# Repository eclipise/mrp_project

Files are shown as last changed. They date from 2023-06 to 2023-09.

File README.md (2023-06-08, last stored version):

# Program Overview

The program’s GUI is implemented with PySimpleGUI in the `GUI` class of the `remote_app.py` file, which is also the main file to run for the remote application. When run, it creates a new object `gui` of the `GUI` class, which internally creates an object `client` of the `Client` class. On creation, `gui` generates a popup window prompting for the IP address of the server, erroring and re-prompting if the IP address is invalid or cannot be reached. Afterwards, it creates the main GUI window.

When the user presses one of the movement buttons on the GUI, the `gui` object calls the `send_movement` method of `gui.client`, which sends the appropriate movement command to the server using an HTTP POST request to the `/move` endpoint. 

The server is implemented in the `server.py` file using Flask, which is the main file running on the Jetson Nano. Upon receiving a POST to `/move`, the server validates the received JSON, checking that the three required fields, `move`, `turn`, and `duration` are present and in valid ranges (-100 to 100 for `move` and `turn`, greater than 0 for `duration`). If they are not valid, the server responds with code 400 and a list of the errors. If they are valid, the server passes them on to the Arduino using the `send_movement` method of an object `arduino_controller` of class `ArduinoController`, which is implemented in `arduino_controller.py`

The `main.iso` file, running on the Arduino, waits indefinitely for an incoming serial message. When it receives one and takes action, it responds with an arbitrary number of serial messages separated by newlines, ending communication with a sentinel message that begins with `END`. For example, its response may be: 

```
Status: Moving robot with command <speed: 100, turn: 0, duration: 200>\n
Info: Left motor speed: 255; right motor speed: 255\n
Status: Robot stopped\n
END: Success\n
```

Or, on failure:

```
Status: Moving robot with command <speed: -100, turn: 0, duration: 200>\n
Abort: Back is not clear\n
END: Failure\n
```

`ArduinoController` continues monitoring the serial connection and catching messages until it receives the sentinel message. 

On receiving a command in its `loop` function, the Arduino performs its own checks on the values (which is redundant but good practice). If the values fail this check, the Arduino responds with the errors and waits for another message. If they pass, it calls its own `moveRobot` function, which checks if the robot is clear to move and moves it if it is. The duration of the movement command is handled by a loop that iterates every 10 ms, stopping the robot if it is no longer clear to move or if the current time is at least `duration` ms from the time the movement started. If the movement completed uninterrupted, `moveRobot` returns 0, else it returns 1 (which `loop` uses to determine whether to send "END: Success" or "END: Failure").

The logic that checks if the robot is clear to move is in `main.ino`'s `frontClear`, `backClear`, and `areaClear` functions, which each update the data from the IR sensors before executing. `frontClear` checks if the front left and right sensors are clear to 30 cm, and if the front center sensor is clear to 20 cm. `backClear` checks if the rear left and right sensors are clear to 30 cm. `areaClear` is used for turning and checks if all sensors are clear to 10 cm. These three functions are called from the `checkClear` function, which takes `speed` and `turn` values and performs the appropriate check based on them. 

After the Arduino finishes and `ArduinoController` receives the sentinel message, it returns a list of the messages to the server, which sends them back to the client using an HTTP response with code 200. The client passes them unchanged to the GUI, which at present prints them to the console.

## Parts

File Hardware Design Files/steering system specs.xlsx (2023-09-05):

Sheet: Motor Specs 6in wheels
Parameters | # | Units |  |  |  |  |  | Input Value
Weight of robot: | 200 | lbs | 90.70 | kg |  |  |  | Output Value
Max Speed: | 100 | ft/min | 1.666666667 | ft/s | 0.508 | m/s
Max incline to climb: | 5 | degrees
Reach max speed in seconds: | 1 | s | 0.508 | m/s^2
Drive wheel diameter: | 6 | in | 3 | in (radius) | 0.0762 | m (radius)
Torque: | 9.41 | Nm | 83.39548646 | in-lbs | 96.0004059 | kg.cm
Per motor with 2 drive motors | 4.707211903 | Nm | 41.69774323 | in-lbs | 48.00020295 | kg.cm
Per motor with 4 drive motors | 2.353605951 | Nm | 20.84887162 | in-lbs | 24.00010148 | kg.cm
rotational speed: | 63.66197724 | RPM | 6.666666667 | rad/sec
Power: | 62.76282537 | watts
Horsepower: | 0.08413247369
Horsepower per motor, 2WD | 0.04206623684
Horsepower per motor, 4WD | 0.02103311842
For payload |  |  |  |  | For incline |  |  |  | For speed
Selected motor torque: | 2.5 | Nm |  |  | Selected motor torque: | 2.5 | Nm |  | Selected motor torque: | 2.5 | Nm
robot acceleration: | 0.5 | m/s2 |  |  | robot acceleration: | 0.05 | m/s2 |  | robot acceleration: | 2 | m/s2
incline angle: | 2.5 | degrees |  |  | incline angle: | 20 | degrees |  | incline angle: | 5 | degrees
wheel radius: | 0.0762 | m |  |  | wheel radius: | 0.1524 | m |  | wheel radius: | 0.1524 | m
safty factor: | 1.5 |  |  |  | safty factor: | 1.5 |  |  | safty factor: | 1.5
1WD Robot weight: | 51.99989936 | lbs |  |  | 1WD Robot weight: | 7.088656484 | lbs |  | 1WD Robot weight: | 8.448880979 | lbs
2WD Robot weight: | 103.9997987 | lbs |  |  | 2WD Robot weight: | 14.17731297 | lbs |  | 2WD Robot weight: | 16.89776196 | lbs
4WD Robot weight: | 207.9995974 | lbs |  |  | 4WD Robot weight: | 28.35462593 | lbs |  | 4WD Robot weight: | 33.79552391 | lbs
Citation: | https://www.servomagazine.com/magazine/article/tips_for_selecting_dc_motors_for_your_mobile_robot

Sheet: Battery Size
Item name | mA | Quantity | Parts total
Motors | 3500 | 4 | 14000
computer | 3000 | 1 | 3000 |  | Battery capacity (mAh) | 30000
wifi chip | computer | 1 |  |  | Battery life (hr): | 1.488833747
ir sensor | 30 | 5 | 150
laser scanner | computer | 1
Arduino | 3000 | 1 | 3000
 |  | total | 20150 | mA
 |  |  | assuming everything is running at max

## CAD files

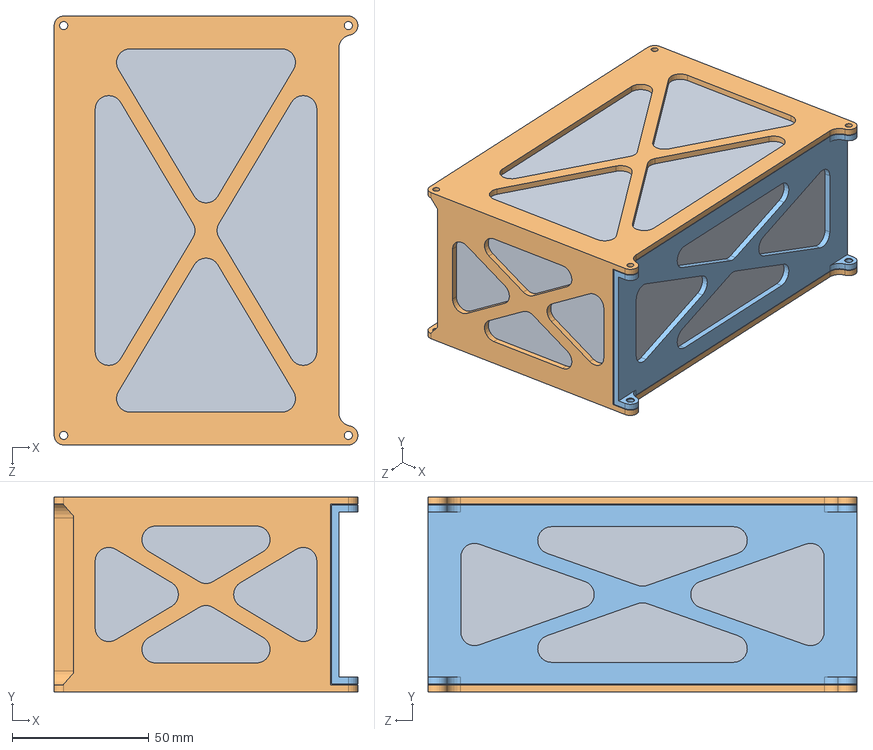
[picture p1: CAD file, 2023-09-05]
Hardware Design Files/2.2 Power Management System/2.2.8 LiFePO4 Batteries/BatteryCell.SLDASM
111.1 x 71.3 x 156.9 mm
Battery
BatteryCarrier
BatteryCarrier - Lid

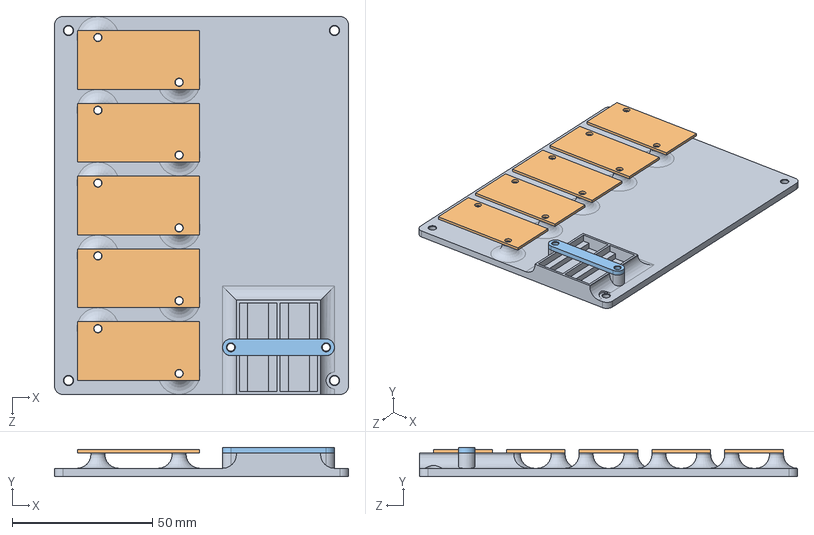
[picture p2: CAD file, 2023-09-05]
Hardware Design Files/2.3 Control System/2.3.1 Buck Converter Assembly/BuckConverter Assembly.SLDASM
105.0 x 10.5 x 135.0 mm
BuckConverterPlate
LM2596 x 5
AmpMeter Bracket

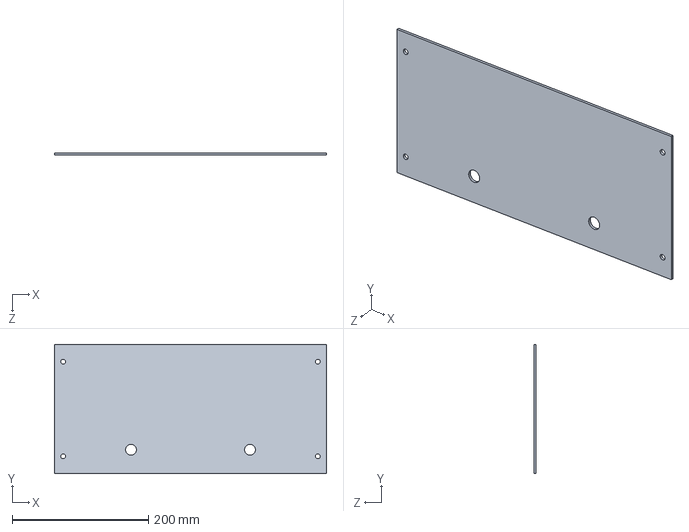
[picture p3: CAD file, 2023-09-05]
Hardware Design Files/2.1 Chassis/2.1.1 Motor Enclosure/SidePlate.SLDPRT
400.0 x 190.0 x 3.17 mm

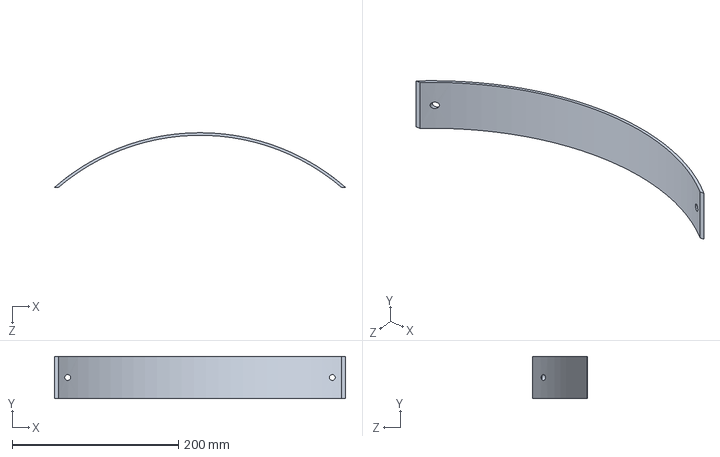
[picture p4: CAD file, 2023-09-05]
Hardware Design Files/2.1 Chassis/2.1.2 Electrical Enclosure/EBack.SLDPRT
350.0 x 50.8 x 65.8 mm

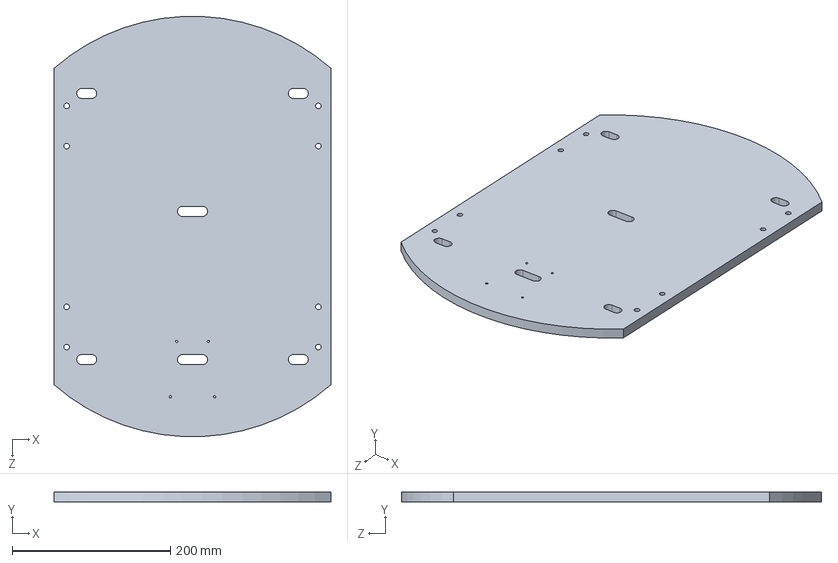
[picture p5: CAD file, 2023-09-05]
Hardware Design Files/2.1 Chassis/2.1.3 LIDAR Plate/1_2inAluminumPlate - LIDARMount.SLDPRT
350.0 x 12.7 x 530.9 mm

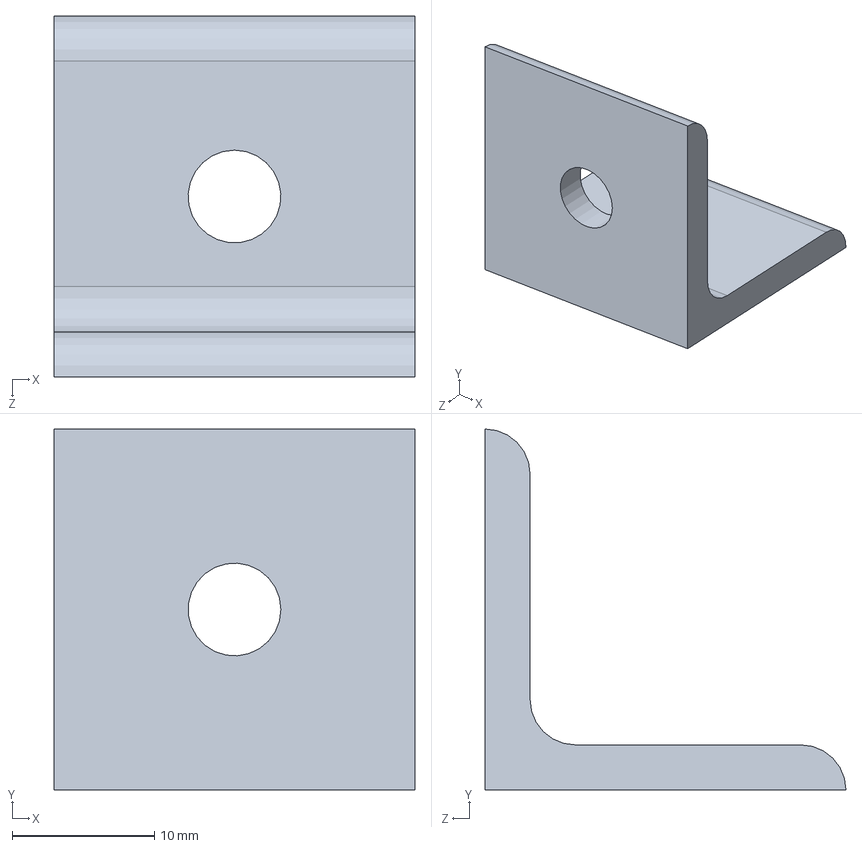
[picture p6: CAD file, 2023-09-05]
Hardware Design Files/2.1 Chassis/8020 - CornerBracket.SLDPRT
25.4 x 25.4 x 25.4 mm

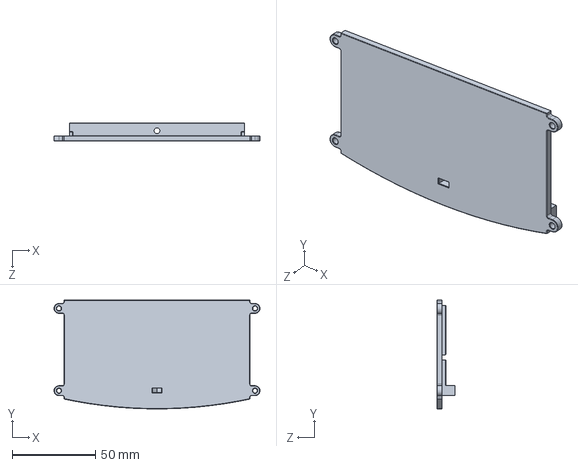
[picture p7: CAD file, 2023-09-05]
Hardware Design Files/2.2 Power Management System/2.2.3 Charger Box Assembly/Charger Box - Lid.SLDPRT
124.0 x 65.5 x 11.0 mm

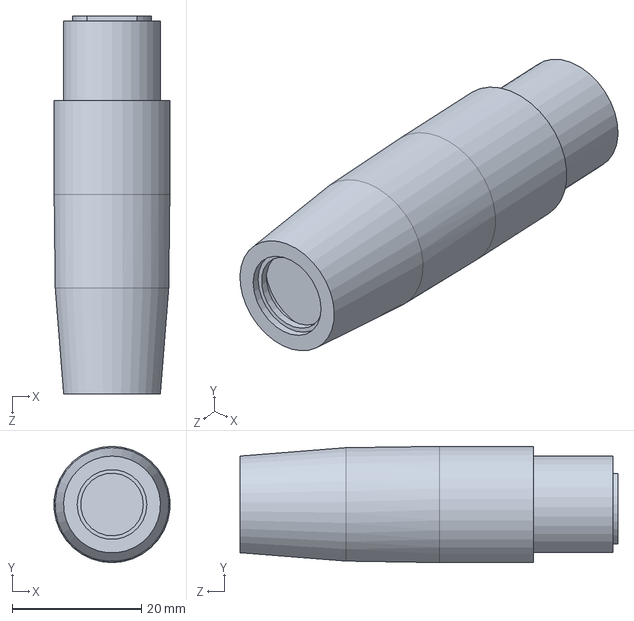
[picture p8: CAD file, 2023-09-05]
Hardware Design Files/2.2 Power Management System/2.2.4-2.2.7 Charger Box Components/XLR Female.SLDPRT
17.9 x 18.0 x 58.5 mm

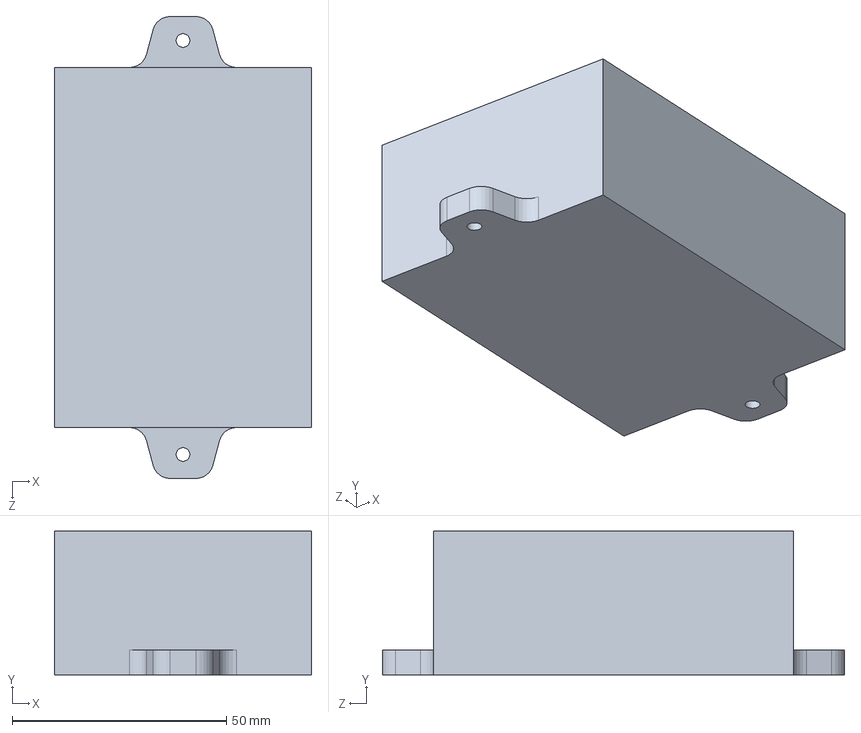
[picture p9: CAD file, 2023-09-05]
Hardware Design Files/2.2 Power Management System/2.2.9 Remote Control Relay Switch/Wireless Relay Switch.SLDPRT
60.0 x 33.6 x 107.8 mm

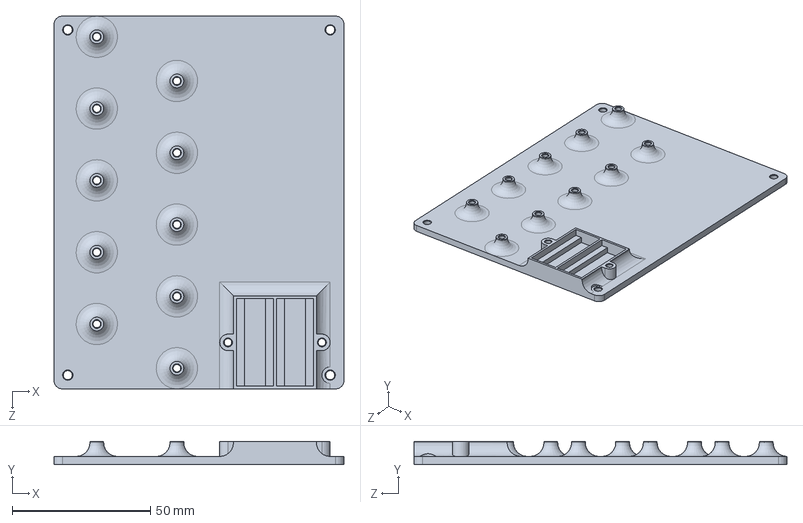
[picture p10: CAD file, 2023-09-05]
Hardware Design Files/2.3 Control System/2.3.1 Buck Converter Assembly/BuckConverterPlate.SLDPRT
105.0 x 8.50 x 135.0 mm

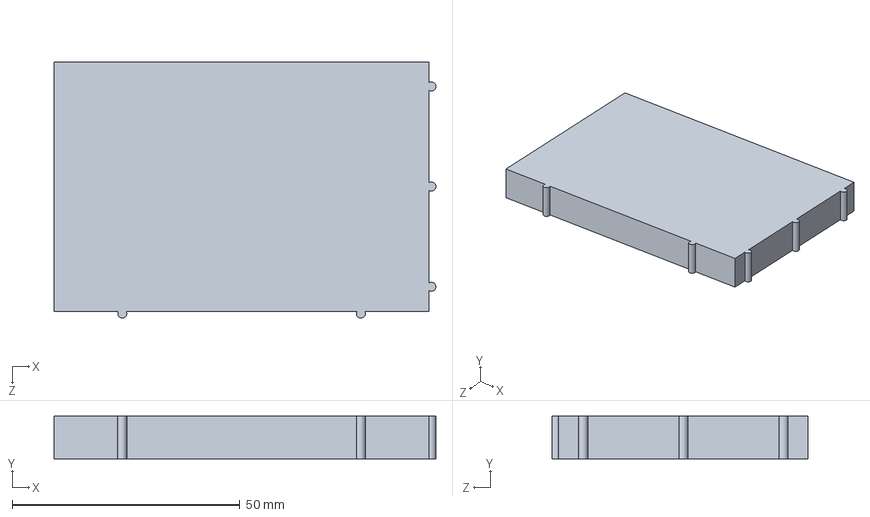
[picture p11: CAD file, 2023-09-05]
Hardware Design Files/2.3 Control System/2.3.2 Arduino Assembly/BreadBoard.SLDPRT
83.9 x 9.40 x 56.3 mm

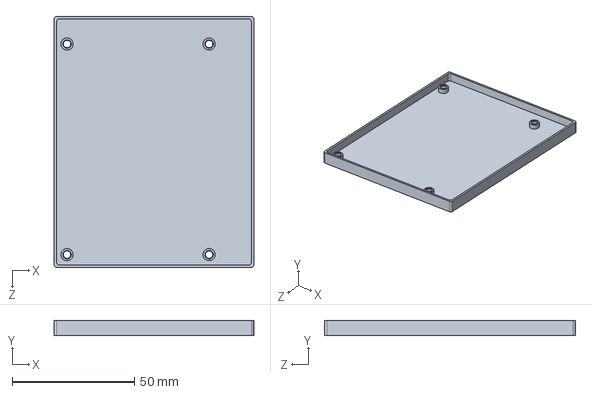
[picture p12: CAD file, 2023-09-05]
Hardware Design Files/2.3 Control System/2.3.3 Jetson Nano/JetsonNano Shroud.SLDPRT
81.5 x 6.00 x 102.5 mm

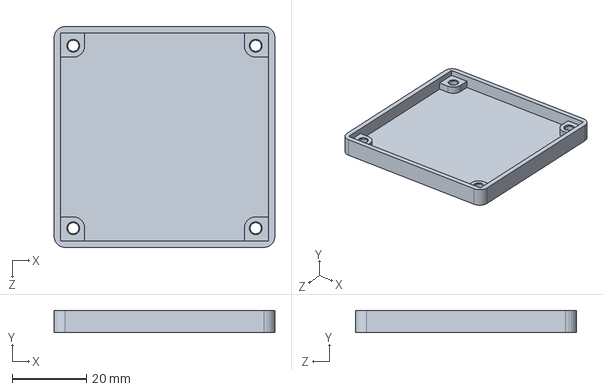
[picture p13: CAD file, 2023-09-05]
Hardware Design Files/2.3 Control System/2.3.4 Motor Control Module/MotorDriver Shroud.SLDPRT
59.3 x 6.00 x 59.3 mm

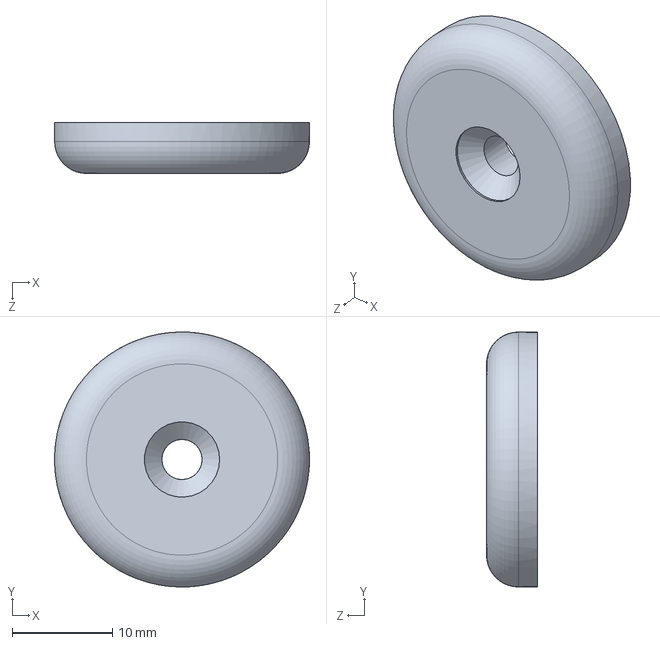
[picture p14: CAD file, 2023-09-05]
Hardware Design Files/2.4 Locomotion System/Wheel End Cap.SLDPRT
25.4 x 25.4 x 5.08 mm

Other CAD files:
Hardware Design Files/2.2 Power Management System/Charger Box Assembly.SLDASM
Hardware Design Files/2.3 Control System/2.3.2 Arduino Assembly/Ardiuno Assembly.SLDASM
Hardware Design Files/2.5 Sensors/Lidar Shroud.SLDPRT
Hardware Design Files/2.5 Sensors/RPLIDAR A1M8 kit/ÎÞÏßÐý×ªÆ½Ì¨1.5.SLDPRT
Hardware Design Files/2.1 Chassis/2.1.1 Motor Enclosure/1_2inAluminumPlate - MotorMount.SLDPRT
Hardware Design Files/2.1 Chassis/2.1.1 Motor Enclosure/Back.SLDPRT
Hardware Design Files/2.1 Chassis/2.1.1 Motor Enclosure/Bottom_AluminumExtrusion.SLDPRT
Hardware Design Files/2.1 Chassis/2.1.1 Motor Enclosure/Front.SLDPRT
Hardware Design Files/2.1 Chassis/2.1.2 Electrical Enclosure/1_2inAluminumPlate - ElectricalMount.SLDPRT
Hardware Design Files/2.1 Chassis/2.1.2 Electrical Enclosure/ESidePlate.SLDPRT
Hardware Design Files/2.1 Chassis/2.1.2 Electrical Enclosure/E_AluminumExtrusion.SLDPRT
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

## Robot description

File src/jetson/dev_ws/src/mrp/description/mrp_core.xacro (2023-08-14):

<?xml version="1.0"?>
<robot xmlns:xacro="http://www.ros.org/wiki/xacro">

    <xacro:include filename="inertial_macros.xacro"/>

    <!-- These are in meters and kilograms -->
    <xacro:property name="chassis_length" value="0.4"/>
    <xacro:property name="chassis_width" value="0.35"/>
    <xacro:property name="chassis_height" value="0.28"/>
    <xacro:property name="chassis_mass" value="30"/> <!-- TODO -->
    <xacro:property name="wheel_radius" value="0.0762"/>
    <xacro:property name="wheel_thickness" value="0.0381"/>
    <xacro:property name="wheel_mass" value="1.5"/> <!-- TODO -->
    <!-- From bottom center -->
    <xacro:property name="wheel_offset_x" value="0.0875"/>
    <xacro:property name="wheel_offset_y" value="${0.1877 + wheel_thickness/2}"/>
    <xacro:property name="wheel_offset_z" value="0.0508"/>

    <!-- Material setup for simulation -->
    <material name="white">
        <color rgba="1 1 1 1"/>
    </material>

    <material name="blue">
        <color rgba="0.2 0.2 1 1"/>
    </material>

    <material name="black">
        <color rgba="0 0 0 1"/>
    </material>

    <material name="red">
        <color rgba="1 0 0 1"/>
    </material>

    <!-- Base link -->
    <link name="base_link">
        
    </link>

    <!-- Base footprint link -->

    <joint name="base_footprint_joint" type="fixed">
        <parent link="base_link"/>
        <child link="base_footprint"/>
        <origin xyz="0 0 0"/>
    </joint>

    <link name="base_footprint">
        
    </link>

    <!-- Chassis -->
    <joint name="chassis_joint" type="fixed">
        <parent link="base_link"/>
        <child link="chassis"/>
        <origin xyz="-${chassis_length/2} 0 0"/>
    </joint>

    <link name="chassis">
        <visual>
            <origin xyz="${chassis_length/2} 0 ${chassis_height/2}"/> <!-- move forward and up half of dimensions, placing origin at rear bottom -->
            <geometry>
                <box size="${chassis_length} ${chassis_width} ${chassis_height}"/>
            </geometry>
            <material name="white"/>
        </visual>
        
        <collision>
            <origin xyz="${chassis_length/2} 0 ${chassis_height/2}"/>
            <geometry>
                <box size="${chassis_length} ${chassis_width} ${chassis_height}"/>
            </geometry>
        </collision>

        <xacro:inertial_box mass="${chassis_mass}" x="${chassis_length}" y="${chassis_width}" z="${chassis_height}">
            <origin xyz="${chassis_length/2} 0 ${chassis_height/2}"/>
        </xacro:inertial_box>
    </link> 

    <gazebo reference="chassis">
        <material>Gazebo/White</material>
    </gazebo>

    <!-- Rear left wheel -->
    <joint name="rear_left_wheel_joint" type="continuous">
        <parent link="base_link"/>
        <child link="rear_left_wheel"/>
        <origin xyz="${-wheel_offset_x} ${wheel_offset_y} ${wheel_offset_z}" rpy="-${pi/2} 0 0"/> <!-- Rotate to be upright -->
        <axis xyz="0 0 1"/> <!-- Direction of rotation -->
    </joint>

    <link name="rear_left_wheel">
        <visual>
            <geometry>
                <cylinder radius="${wheel_radius}" length="${wheel_thickness}"/>
            </geometry>
            <material name="red"/>
        </visual>
        
        <collision>
            <geometry>
                <cylinder radius="${wheel_radius}" length="${wheel_thickness}"/>
            </geometry>
        </collision>

        <xacro:inertial_cylinder mass="${wheel_mass}" radius="${wheel_radius}" length="${wheel_thickness}">
            <origin xyz="0 0 0"/> <!-- No origin given, so set to 0s -->
        </xacro:inertial_cylinder>
    </link>

    <gazebo reference="rear_left_wheel">
        <material>Gazebo/Red</material>
    </gazebo>

    <!-- Rear right wheel -->
    <joint name="rear_right_wheel_joint" type="continuous">
        <parent link="base_link"/>
        <child link="rear_right_wheel"/>
        <origin xyz="${-wheel_offset_x} ${-wheel_offset_y} ${wheel_offset_z}" rpy="${pi/2} 0 0"/>
        <axis xyz="0 0 -1"/>
    </joint>

    <link name="rear_right_wheel">
        <visual>
            <geometry>
                <cylinder radius="${wheel_radius}" length="${wheel_thickness}"/>
            </geometry>
            <material name="red"/>
        </visual>
        
        <collision>
            <geometry>
                <cylinder radius="${wheel_radius}" length="${wheel_thickness}"/>
            </geometry>
        </collision>

        <xacro:inertial_cylinder mass="${wheel_mass}" radius="${wheel_radius}" length="${wheel_thickness}">
            <origin xyz="0 0 0"/>
        </xacro:inertial_cylinder>
    </link>

    <gazebo reference="rear_right_wheel">
        <material>Gazebo/Red</material>
    </gazebo>

    <!-- Front left wheel -->
    <joint name="front_left_wheel_joint" type="continuous">
        <parent link="base_link"/>
        <child link="front_left_wheel"/>
        <origin xyz="${wheel_offset_x} ${wheel_offset_y} ${wheel_offset_z}" rpy="-${pi/2} 0 0"/>
        <axis xyz="0 0 1"/>
    </joint>

    <link name="front_left_wheel">
        <visual>
            <geometry>
                <cylinder radius="${wheel_radius}" length="${wheel_thickness}"/>
            </geometry>
            <material name="blue"/>
        </visual>
        
        <collision>
            <geometry>
                <cylinder radius="${wheel_radius}" length="${wheel_thickness}"/>
            </geometry>
        </collision>

        <xacro:inertial_cylinder mass="${wheel_mass}" radius="${wheel_radius}" length="${wheel_thickness}">
            <origin xyz="0 0 0"/>
        </xacro:inertial_cylinder>
    </link>

    <gazebo reference="front_left_wheel">
        <material>Gazebo/Blue</material>
    </gazebo>

    <!-- Front right wheel -->
    <joint name="front_right_wheel_joint" type="continuous">
        <parent link="base_link"/>
        <child link="front_right_wheel"/>
        <origin xyz="${wheel_offset_x} ${-wheel_offset_y} ${wheel_offset_z}" rpy="${pi/2} 0 0"/>
        <axis xyz="0 0 -1"/>
    </joint>

    <link name="front_right_wheel">
        <visual>
            <geometry>
                <cylinder radius="${wheel_radius}" length="${wheel_thickness}"/>
            </geometry>
            <material name="blue"/>
        </visual>
        
        <collision>
            <geometry>
                <cylinder radius="${wheel_radius}" length="${wheel_thickness}"/>
            </geometry>
        </collision>

        <xacro:inertial_cylinder mass="${wheel_mass}" radius="${wheel_radius}" length="${wheel_thickness}">
            <origin xyz="0 0 0"/>
        </xacro:inertial_cylinder>
    </link>

    <gazebo reference="front_right_wheel">
        <material>Gazebo/Blue</material>
    </gazebo>

</robot>

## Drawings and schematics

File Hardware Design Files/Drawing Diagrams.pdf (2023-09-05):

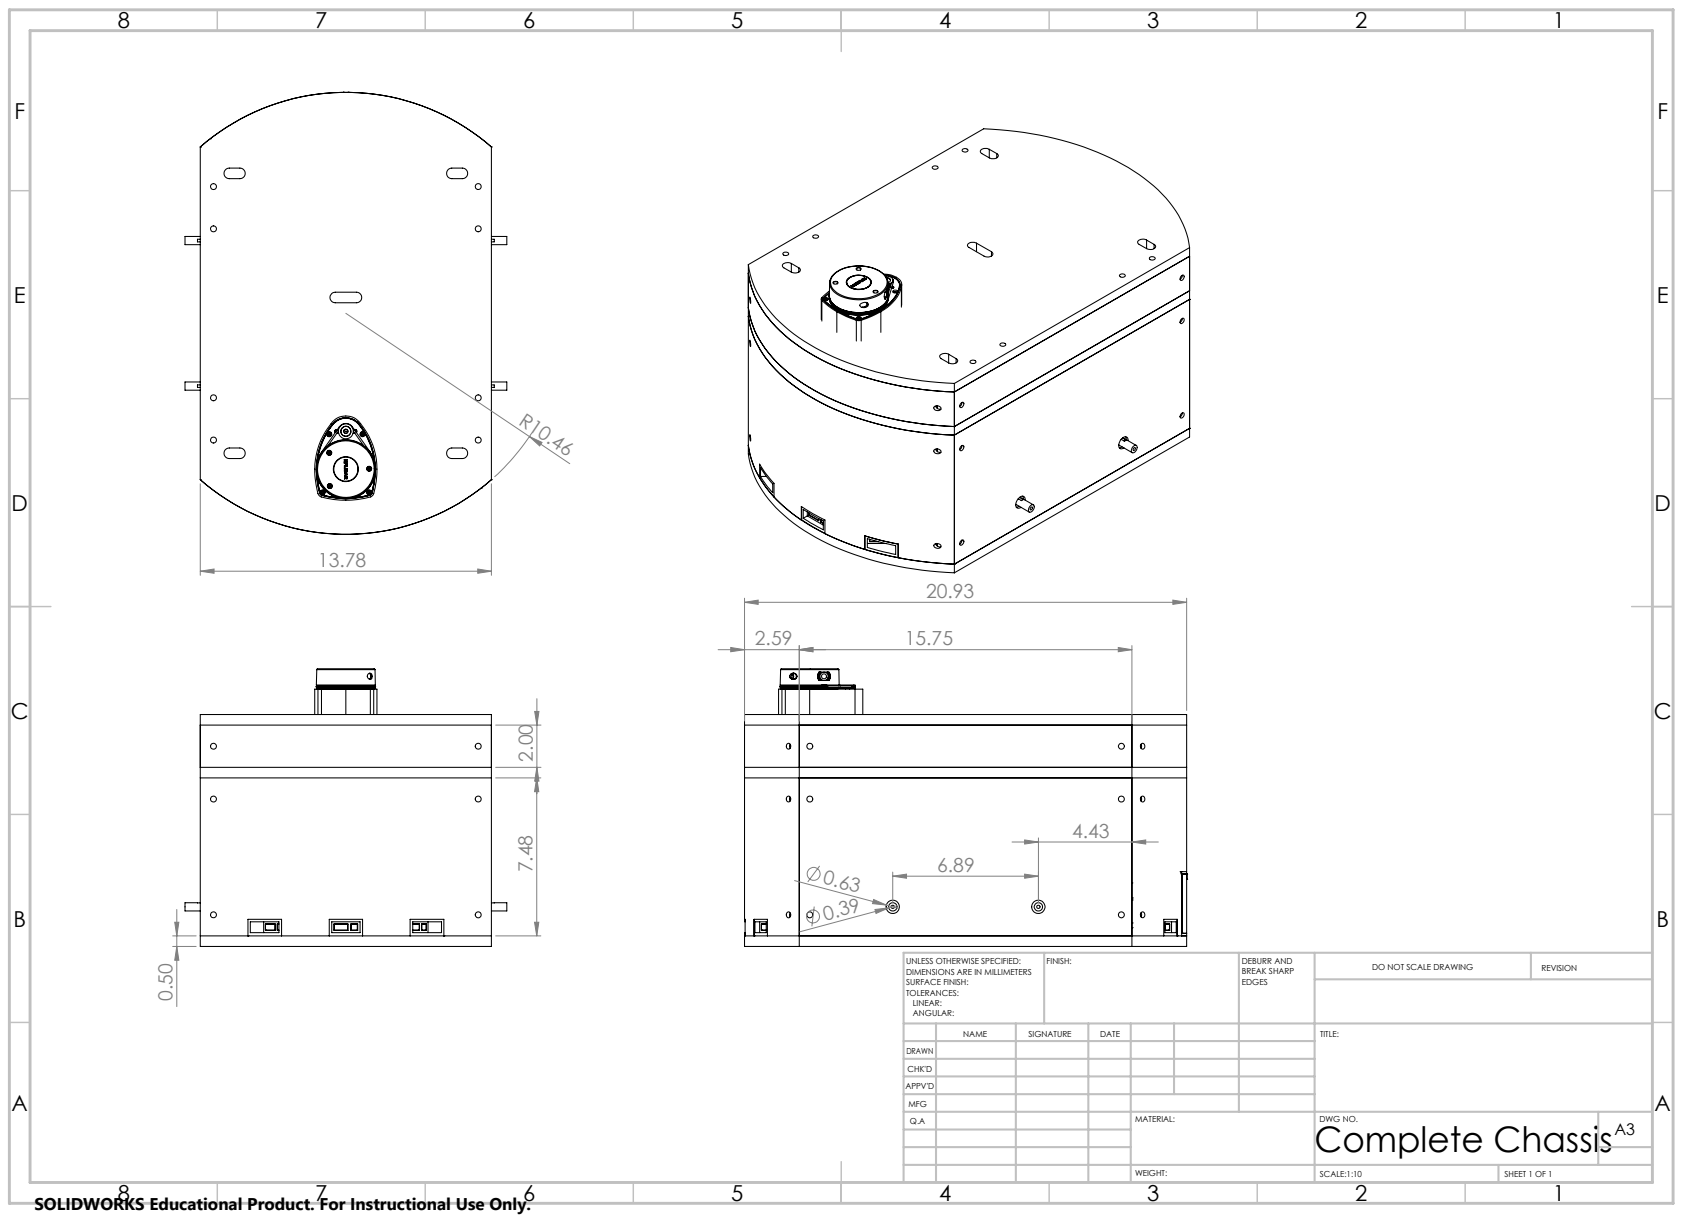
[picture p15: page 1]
FINISH:; DEBURR AND; BREAK SHARP; DO NOT SCALE DRAWING; REVISION; SCALE:1:10; SHEET 1 OF 1

UNLESS OTHERWISE SPECIFIED:
DIMENSIONS ARE IN MILLIMETERS
SURFACE FINISH:
TOLERANCES:
LINEAR:
ANGULAR:

NAME | SIGNATURE | DATE | | | | TITLE:

DRAWN
CHK'D
APPV'D
MFG
Q.A | | | | MATERIAL: | DWG NO. Complete Chassis | A3

SOLIDWORKS Educational Product. For Instructional Use Only.

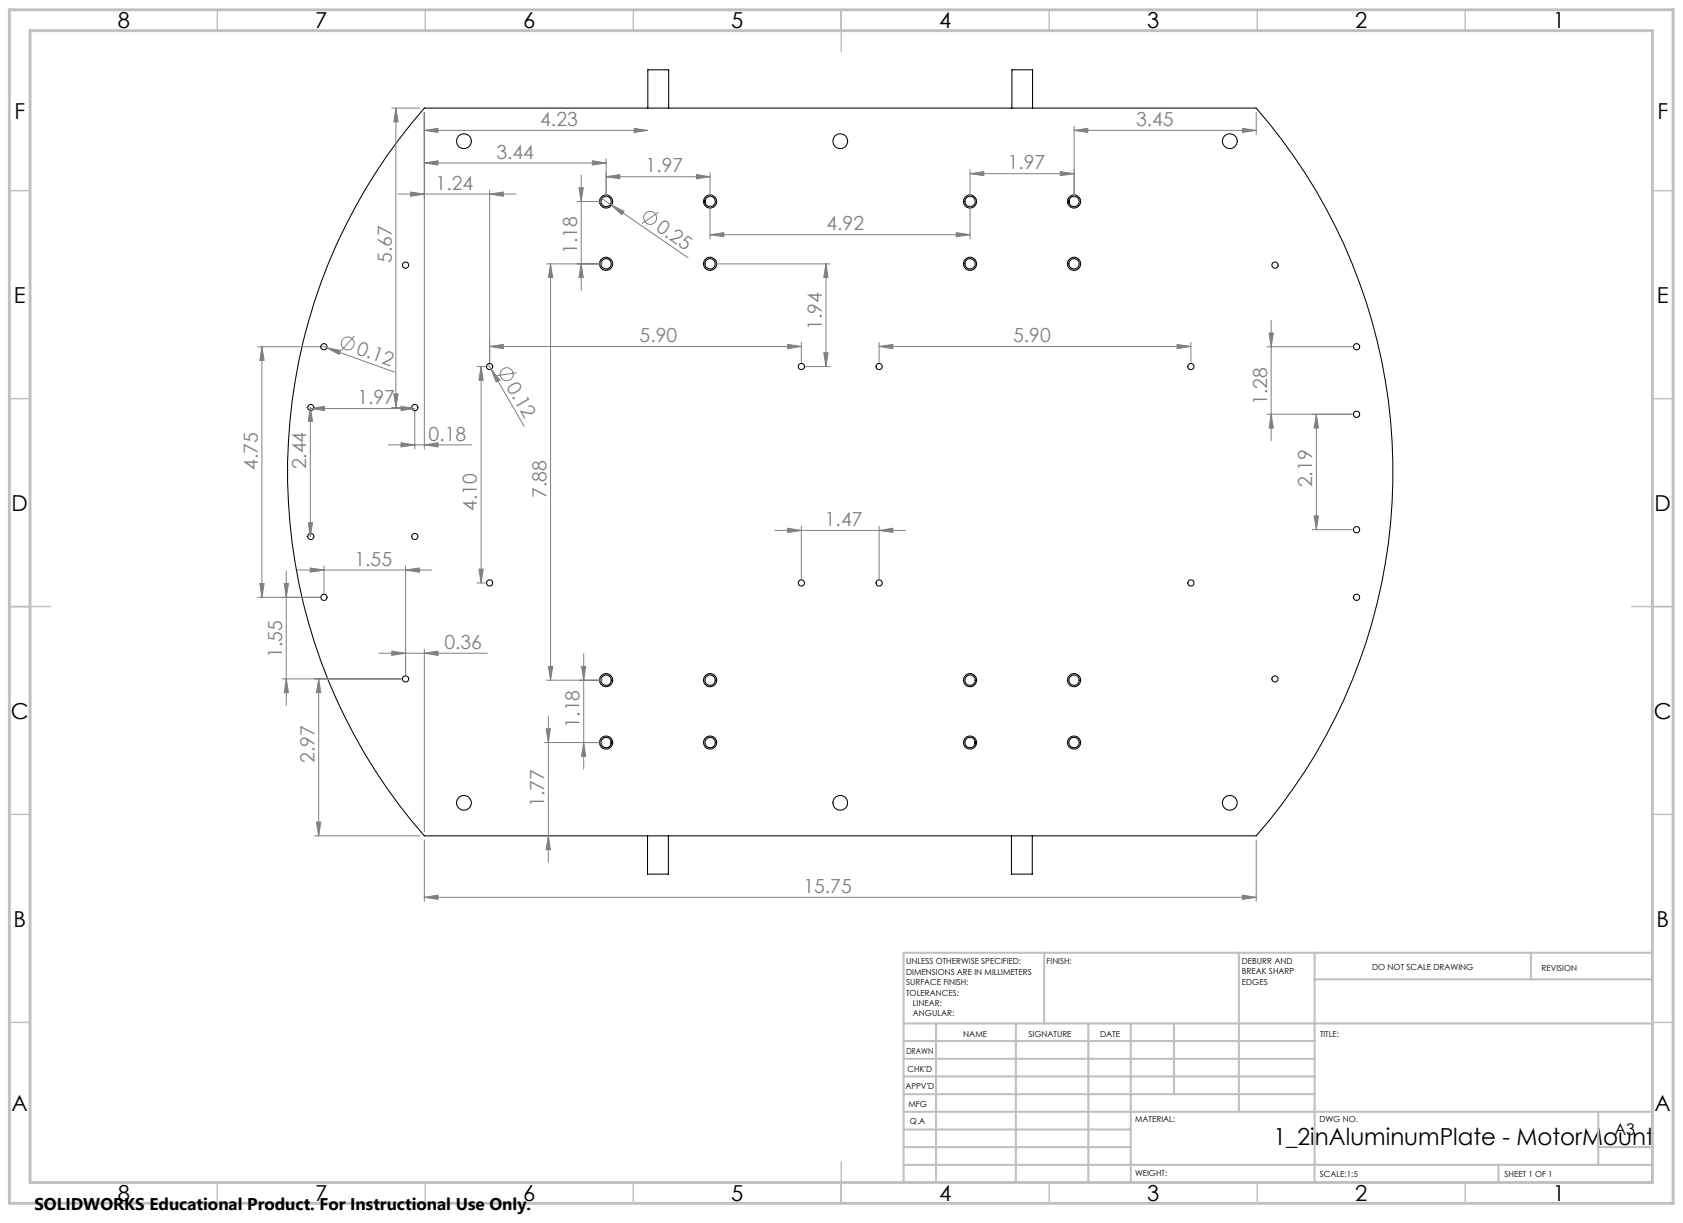
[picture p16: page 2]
FINISH:; DEBURR AND; BREAK SHARP; DO NOT SCALE DRAWING; REVISION

UNLESS OTHERWISE SPECIFIED:
DIMENSIONS ARE IN MILLIMETERS
SURFACE FINISH:
TOLERANCES:
LINEAR:
ANGULAR:

NAME | SIGNATURE | DATE | | | | TITLE:

DRAWN
CHK'D
APPV'D
MFG

1_2inAluminumPlate - MotorMount

SCALE:1:5 | SHEET 1 OF 1

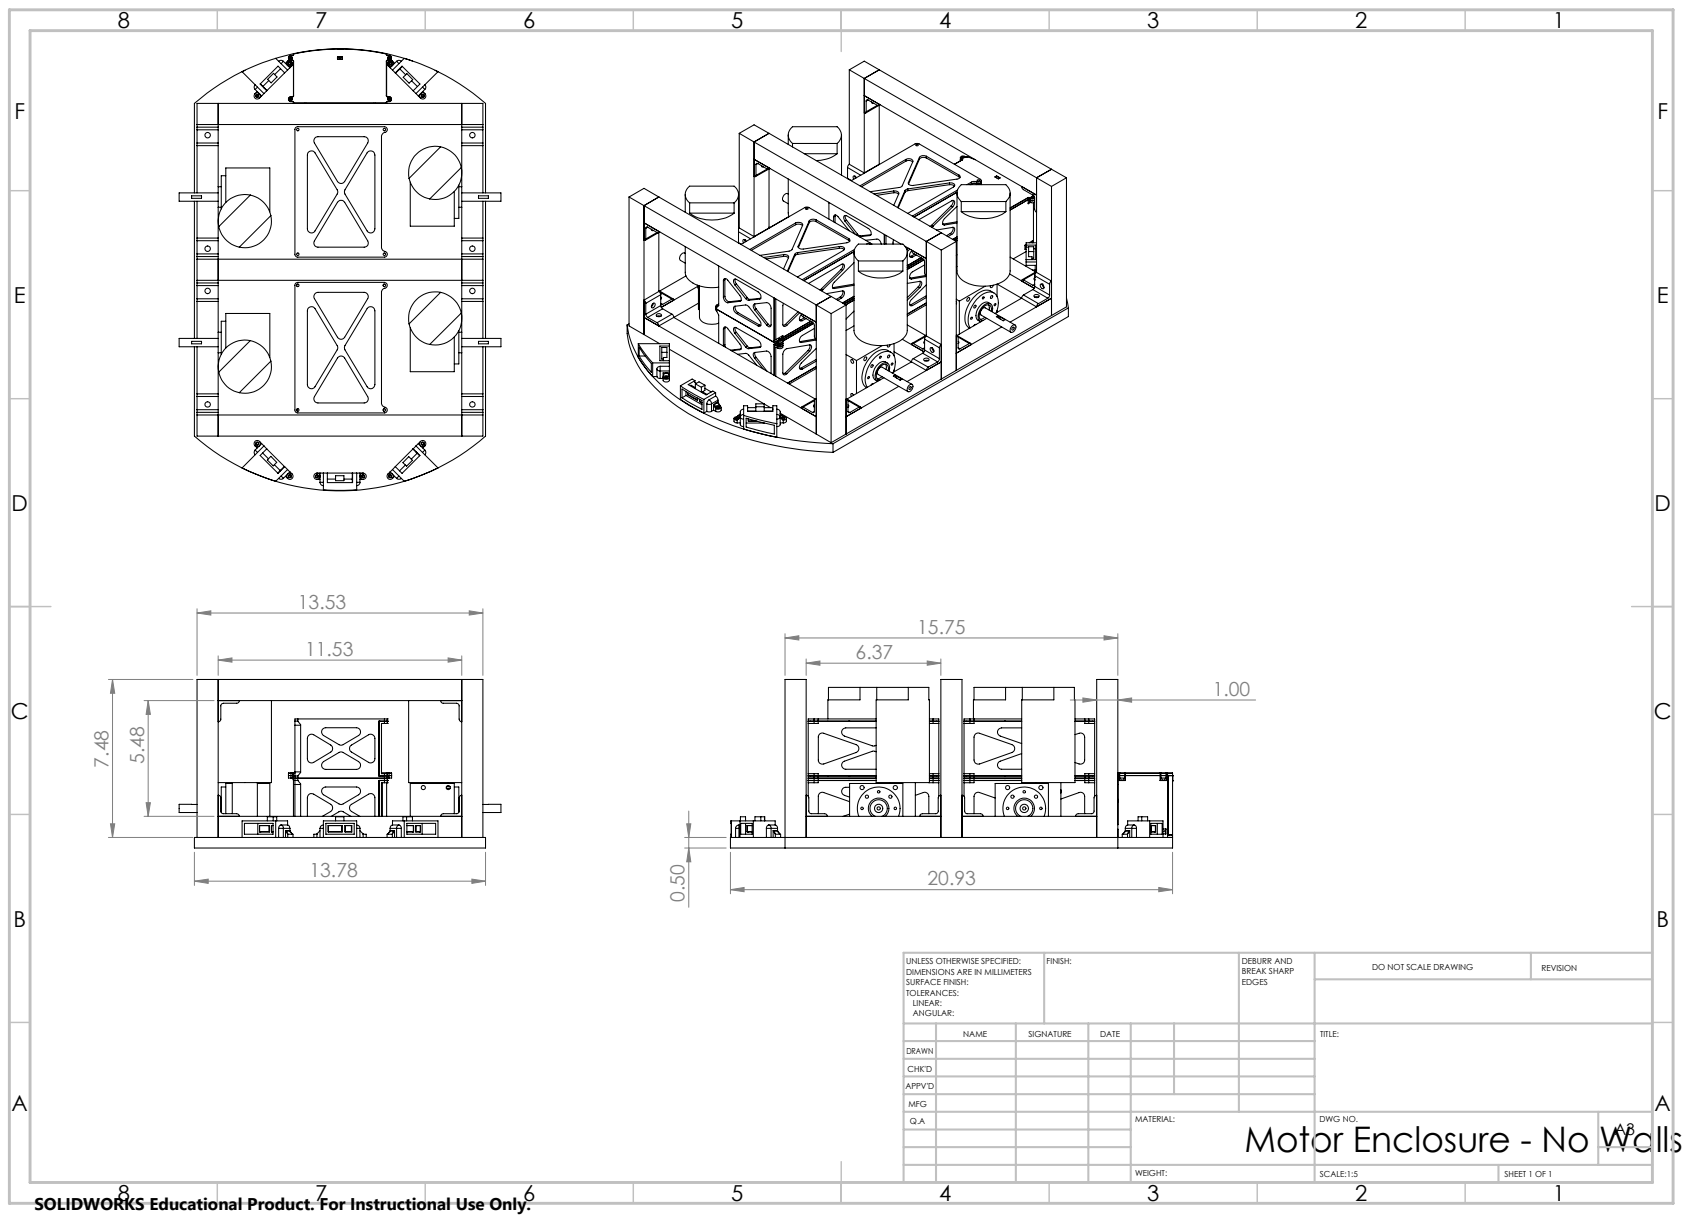
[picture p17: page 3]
FINISH:; DEBURR AND; BREAK SHARP; DO NOT SCALE DRAWING; REVISION

UNLESS OTHERWISE SPECIFIED:
DIMENSIONS ARE IN MILLIMETERS
SURFACE FINISH:
TOLERANCES:
LINEAR:
ANGULAR:

NAME | SIGNATURE | DATE | TITLE:

DRAWN
CHK'D
APPV'D
MFG

Motor Enclosure - No Walls

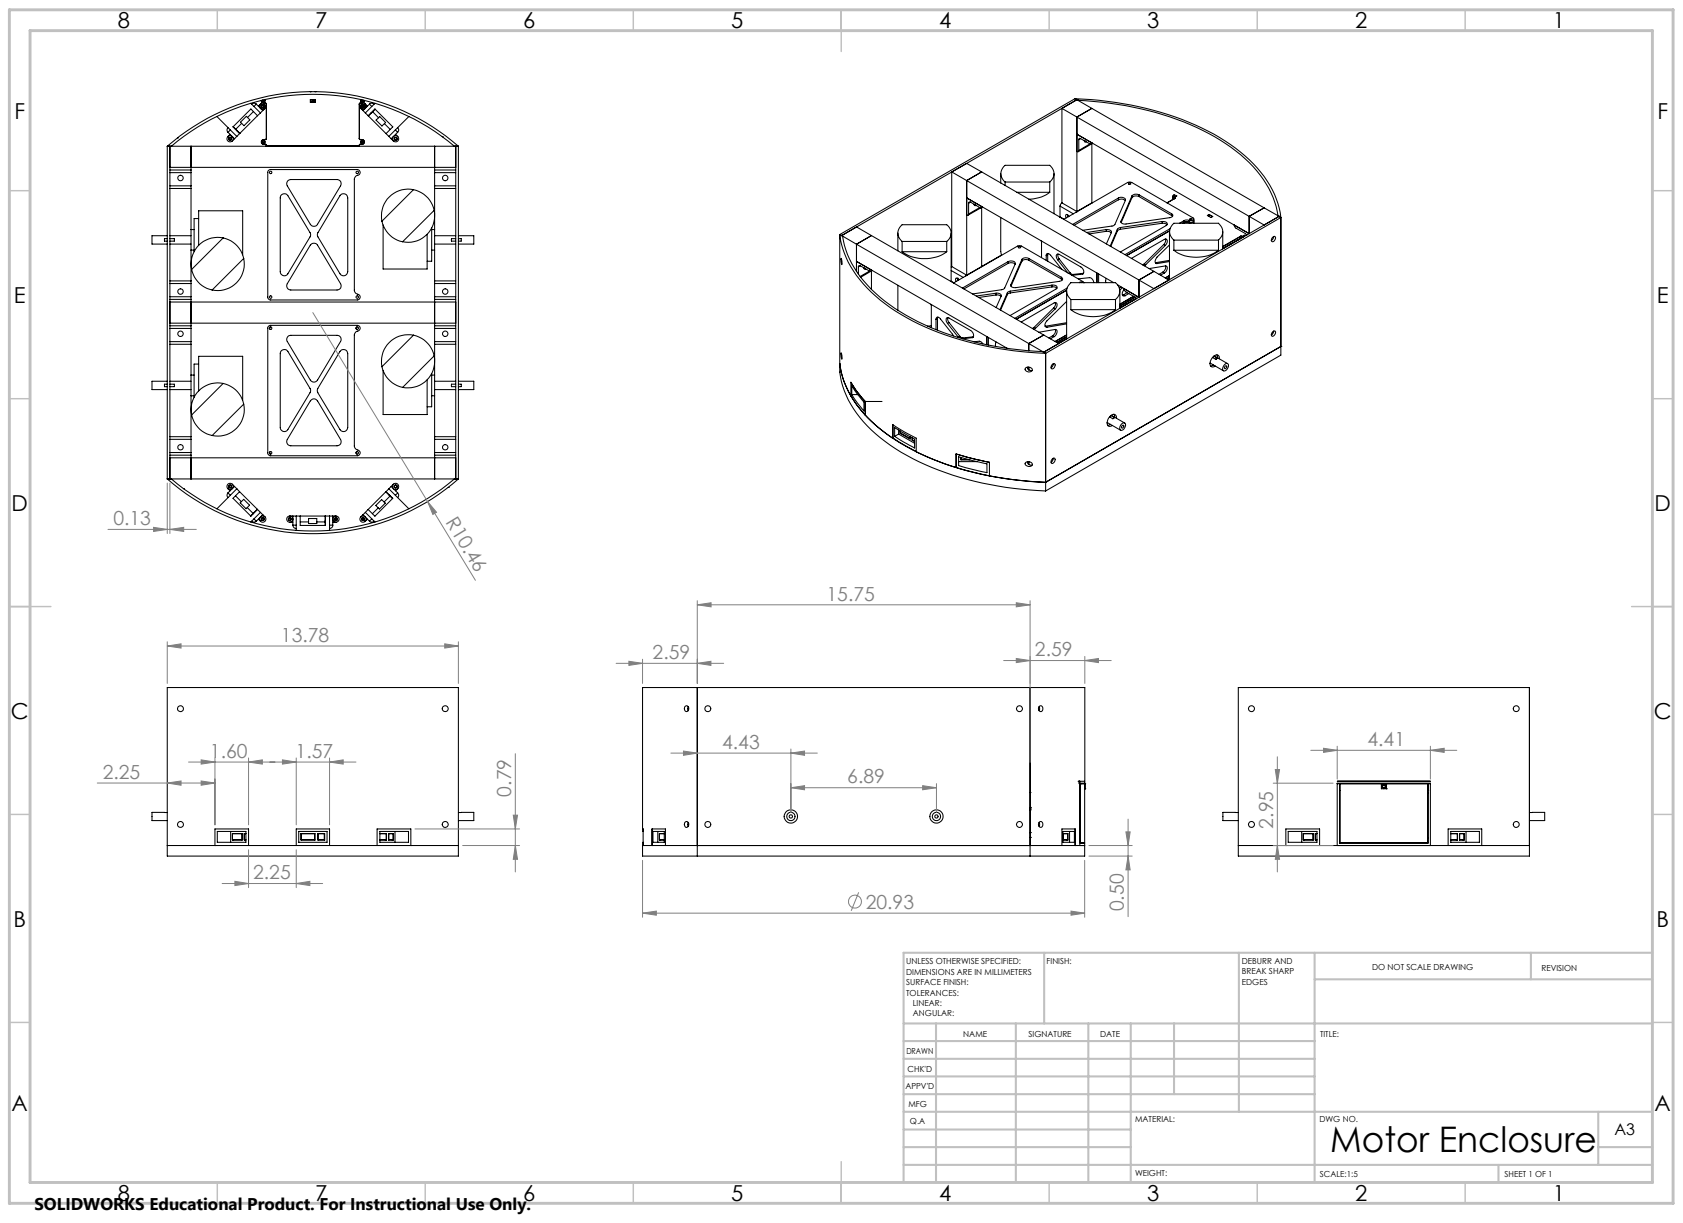
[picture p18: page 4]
FINISH:; DEBURR AND; BREAK SHARP; DO NOT SCALE DRAWING; REVISION

UNLESS OTHERWISE SPECIFIED:
DIMENSIONS ARE IN MILLIMETERS
SURFACE FINISH:
TOLERANCES:
LINEAR:
ANGULAR:

NAME | SIGNATURE | DATE | | TITLE:

DRAWN
CHK'D
APPV'D
MFG

Motor Enclosure

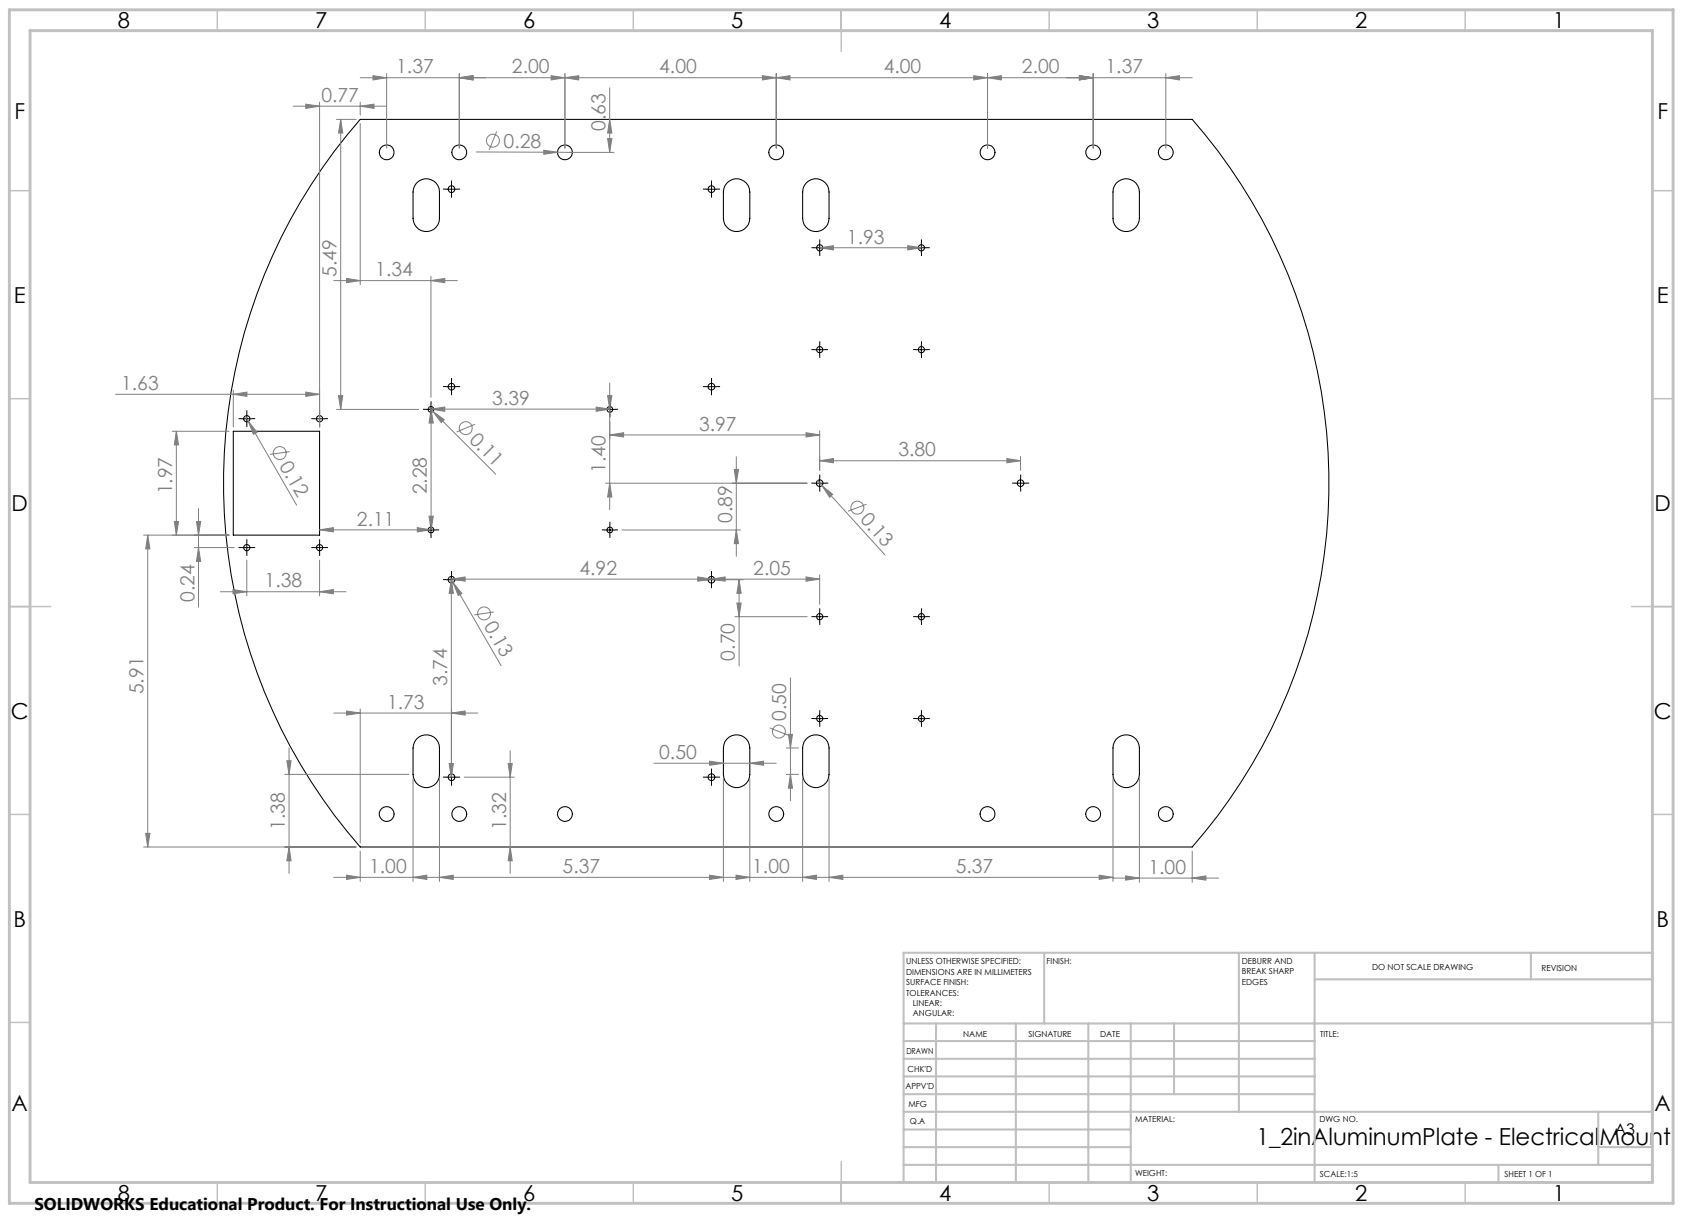
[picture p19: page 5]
FINISH:; DEBURR AND; BREAK SHARP; DO NOT SCALE DRAWING; REVISION

UNLESS OTHERWISE SPECIFIED:
DIMENSIONS ARE IN MILLIMETERS
SURFACE FINISH:
TOLERANCES:
LINEAR:
ANGULAR:

NAME | SIGNATURE | DATE | | TITLE:

DRAWN
CHK'D
APPV'D
MFG

1_2inAluminumPlate - ElectricalMount

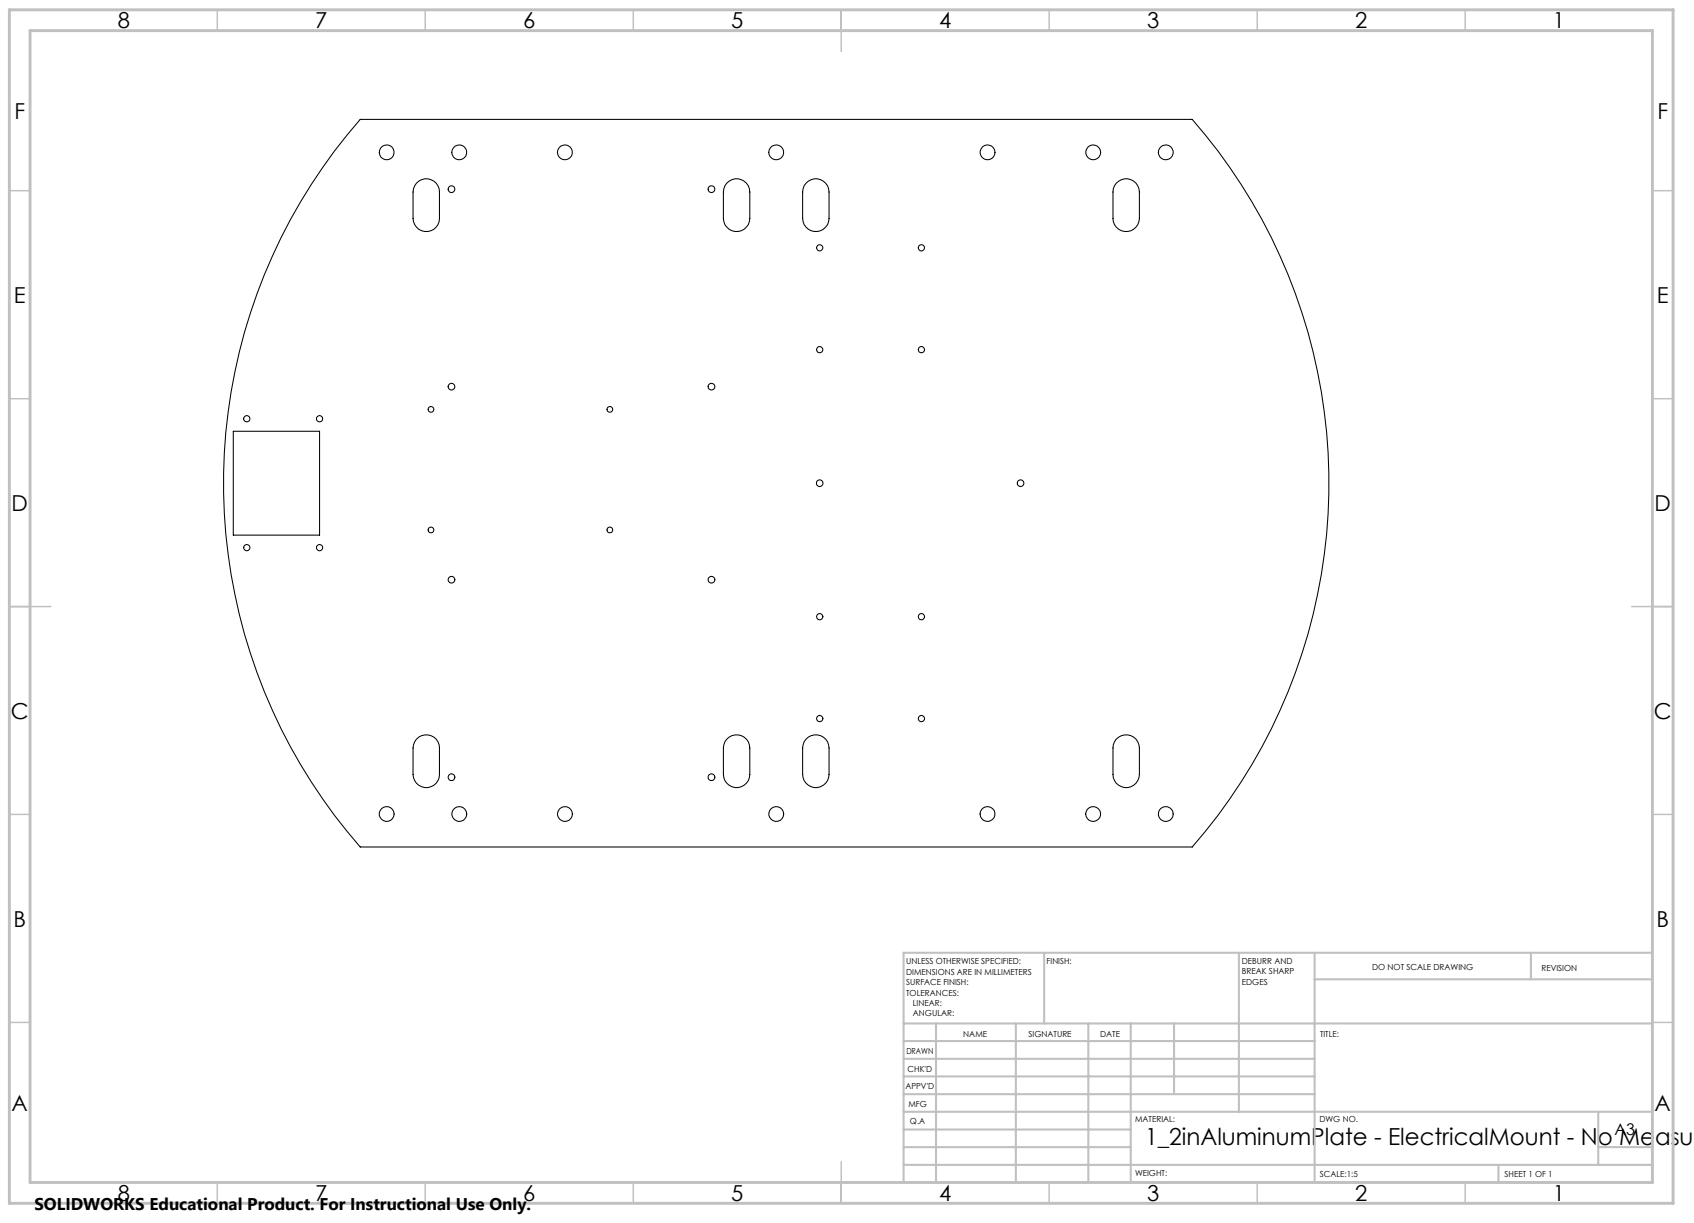
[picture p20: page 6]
FINISH:; DEBURR AND; BREAK SHARP; DO NOT SCALE DRAWING; REVISION

UNLESS OTHERWISE SPECIFIED:
DIMENSIONS ARE IN MILLIMETERS
SURFACE FINISH:
TOLERANCES:
LINEAR:
ANGULAR:

NAME | SIGNATURE | DATE | TITLE:

DRAWN
CHK'D
APPV'D
MFG

1_2inAluminumPlate - ElectricalMount - No Measurements

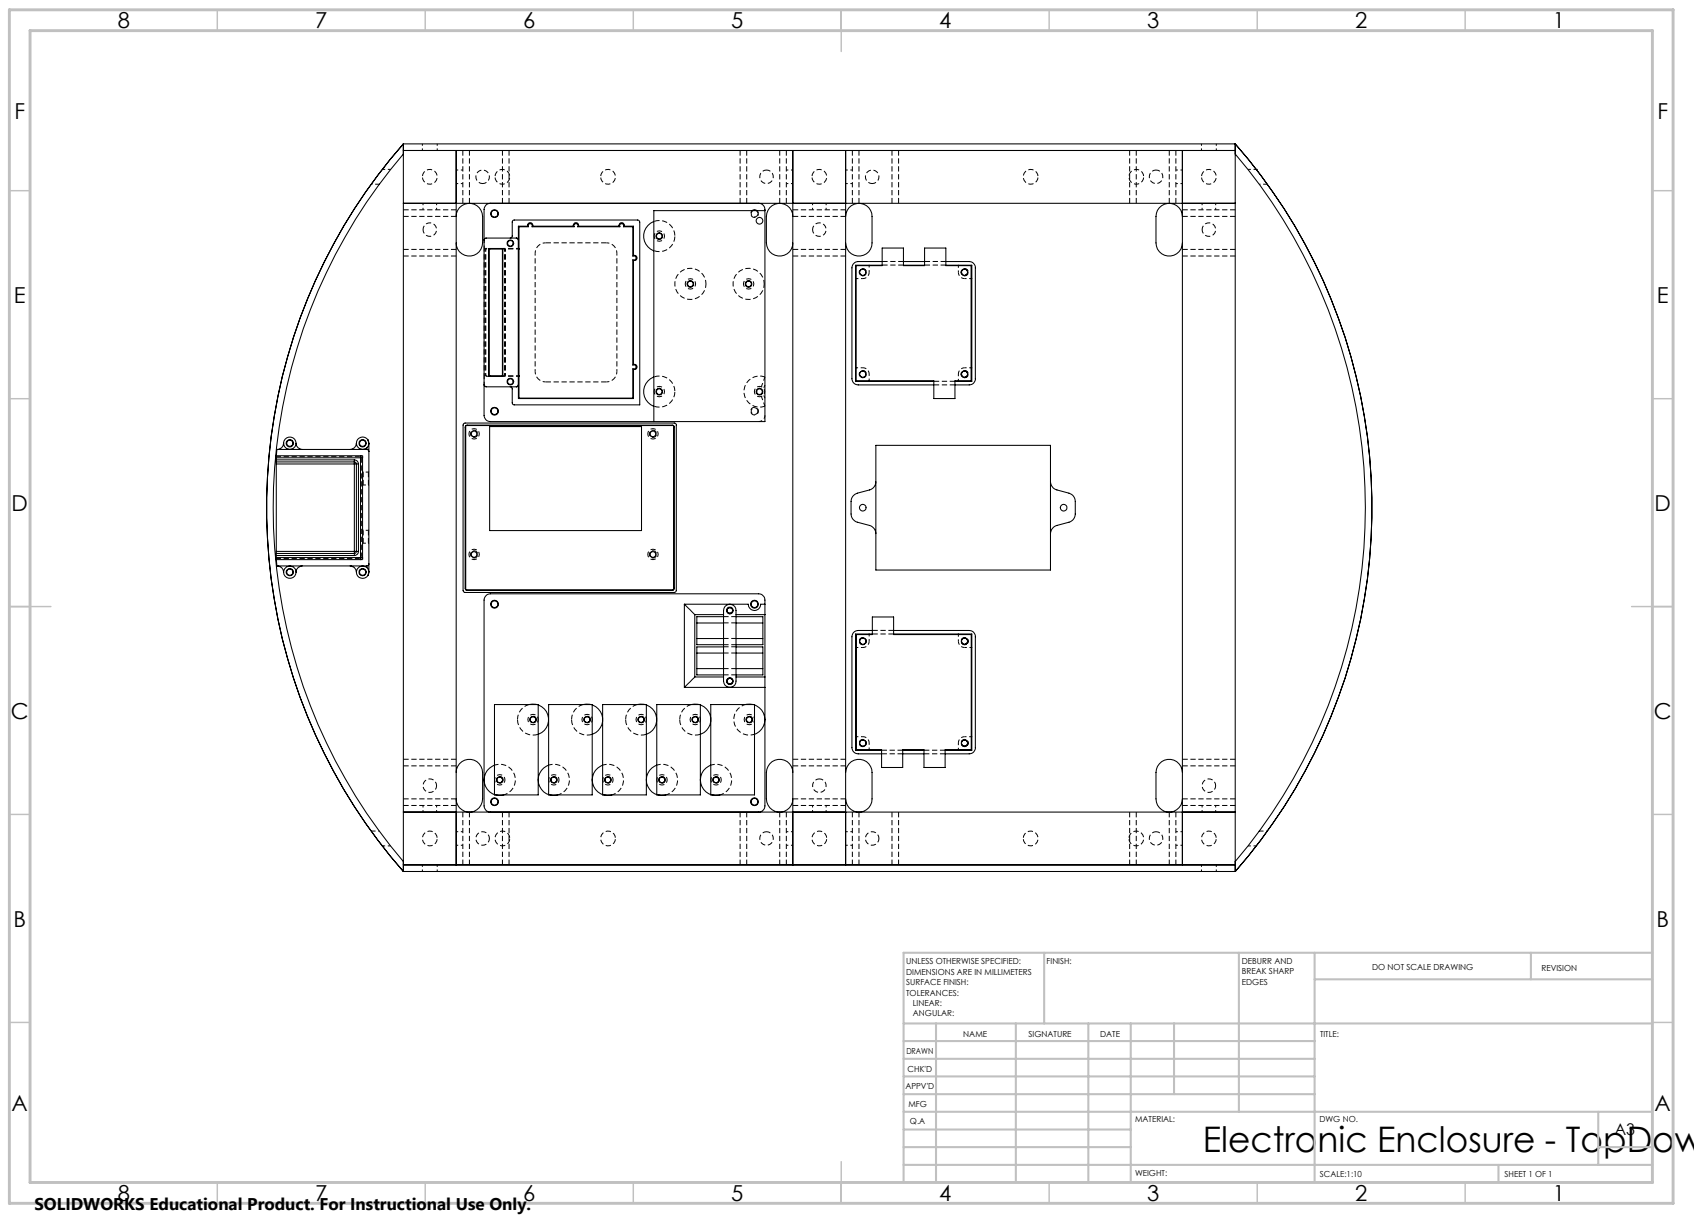
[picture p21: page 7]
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

UNLESS OTHERWISE SPECIFIED:
DIMENSIONS ARE IN MILLIMETERS
SURFACE FINISH:
TOLERANCES:
LINEAR:
ANGULAR:

NAME | SIGNATURE | DATE | TITLE:

DRAWN
CHK'D
APPV'D
MFG

Electronic Enclosure - TopDown

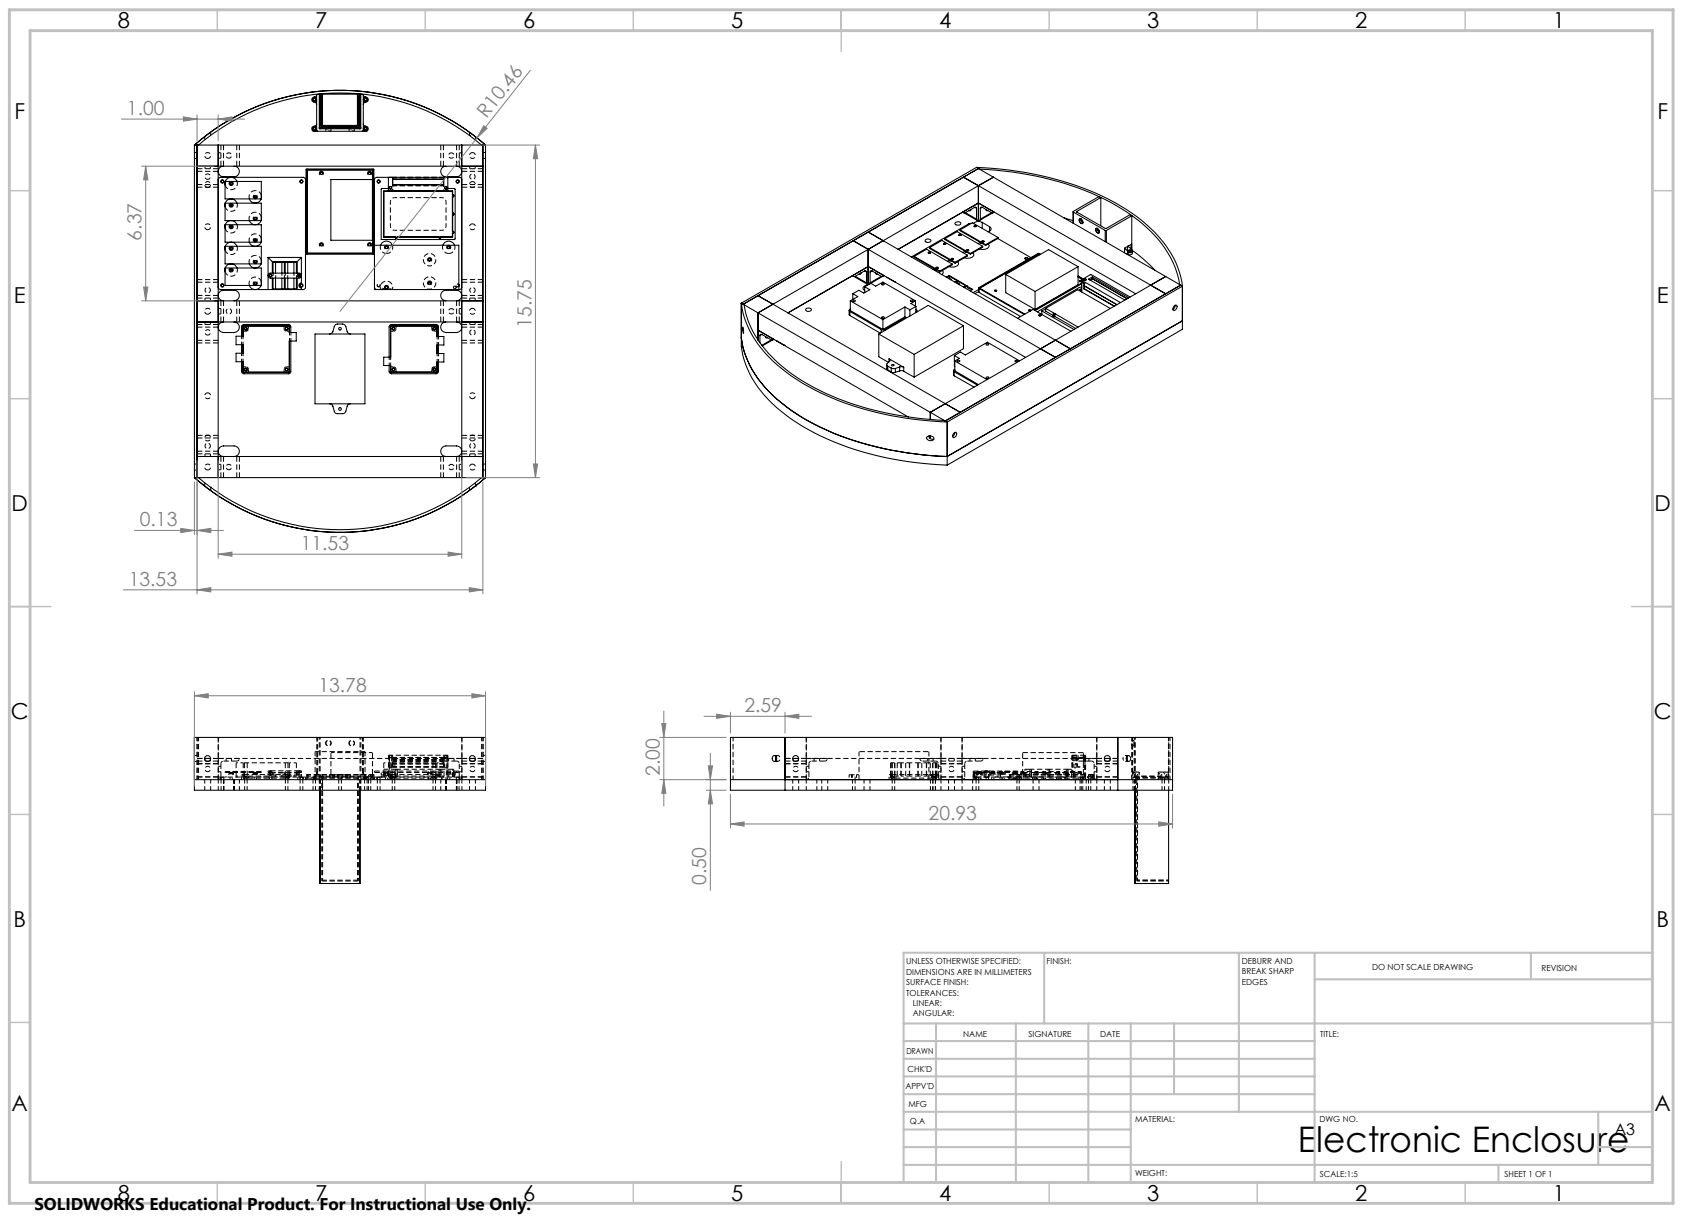
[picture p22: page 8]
FINISH:; DEBURR AND; BREAK SHARP; DO NOT SCALE DRAWING; REVISION

UNLESS OTHERWISE SPECIFIED:
DIMENSIONS ARE IN MILLIMETERS
SURFACE FINISH:
TOLERANCES:
LINEAR:
ANGULAR:

NAME | SIGNATURE | DATE | | TITLE:

DRAWN
CHK'D
APPV'D
MFG

Electronic Enclosure

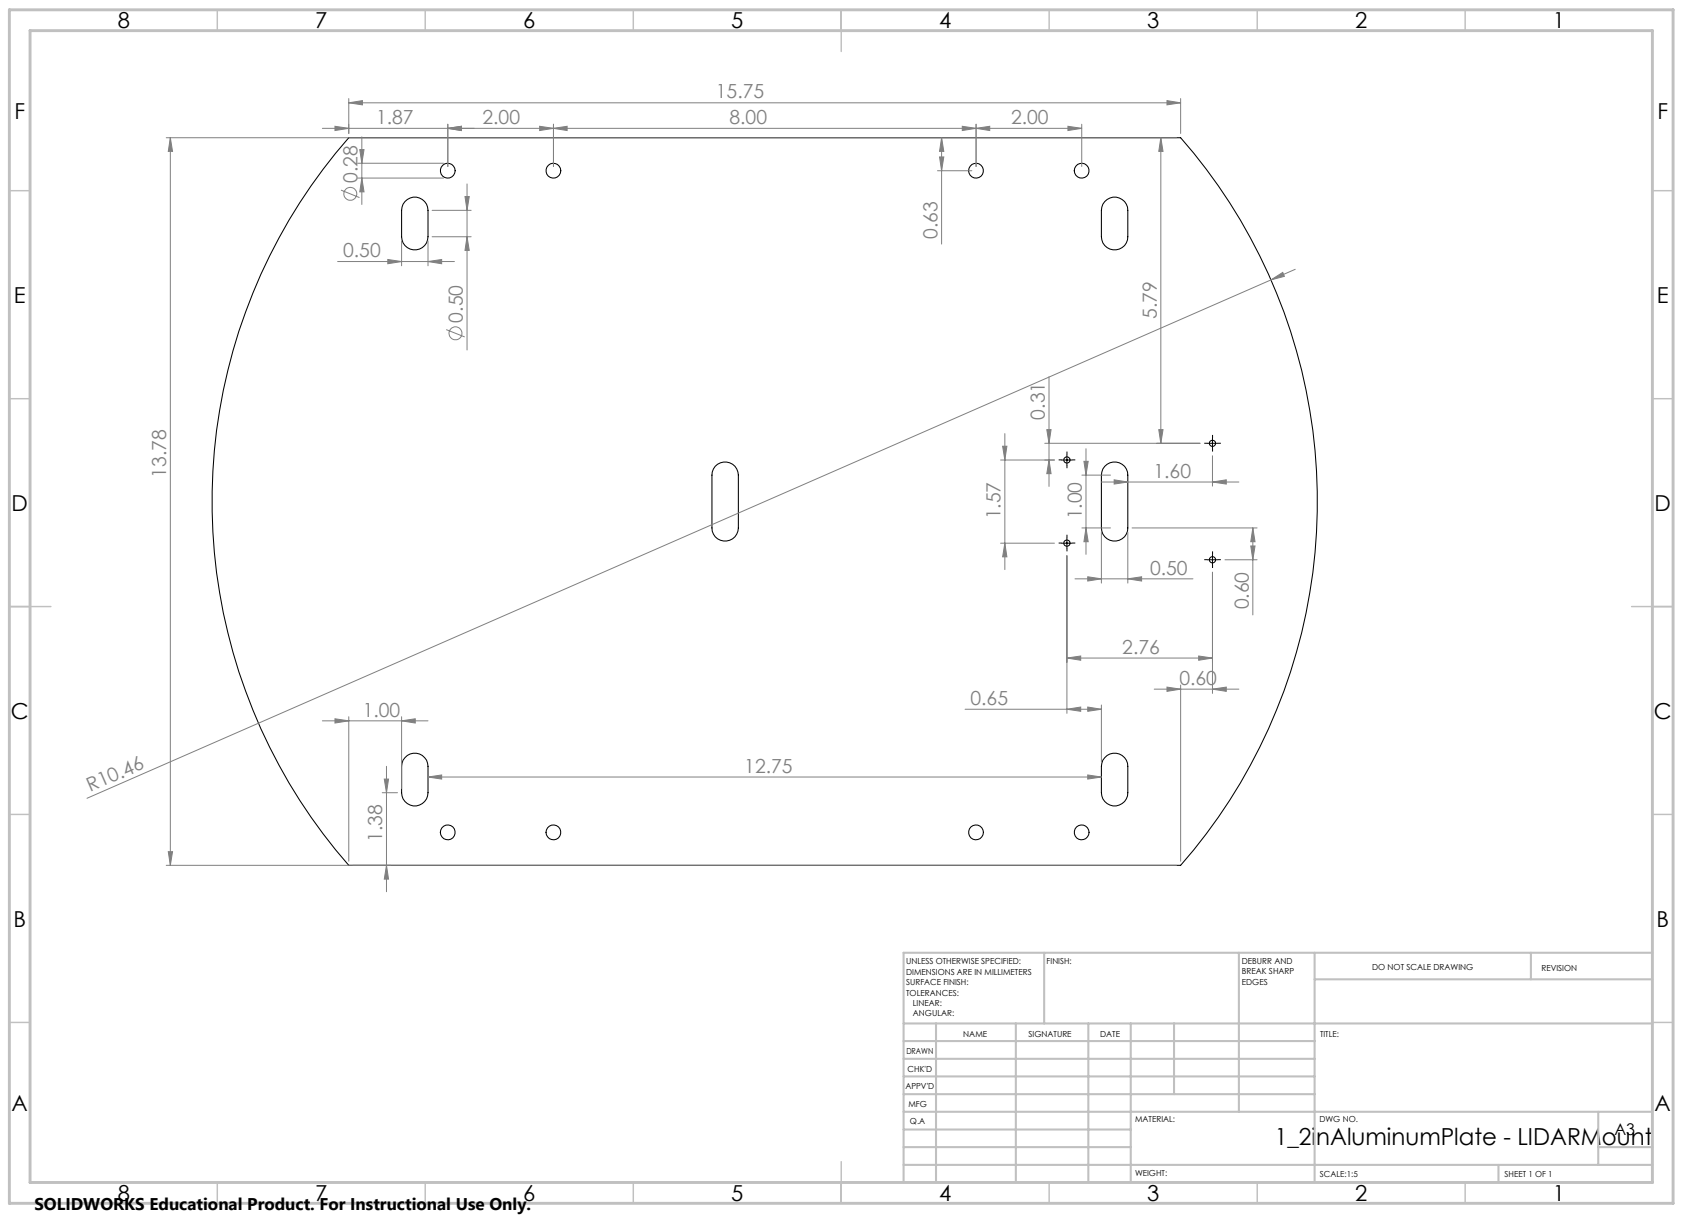
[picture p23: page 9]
FINISH:; DEBURR AND; BREAK SHARP; DO NOT SCALE DRAWING; REVISION

UNLESS OTHERWISE SPECIFIED:
DIMENSIONS ARE IN MILLIMETERS
SURFACE FINISH:
TOLERANCES:
LINEAR:
ANGULAR:

NAME | SIGNATURE | DATE | | TITLE:

DRAWN
CHK'D
APPV'D
MFG

1_2inAluminumPlate - LIDARMount

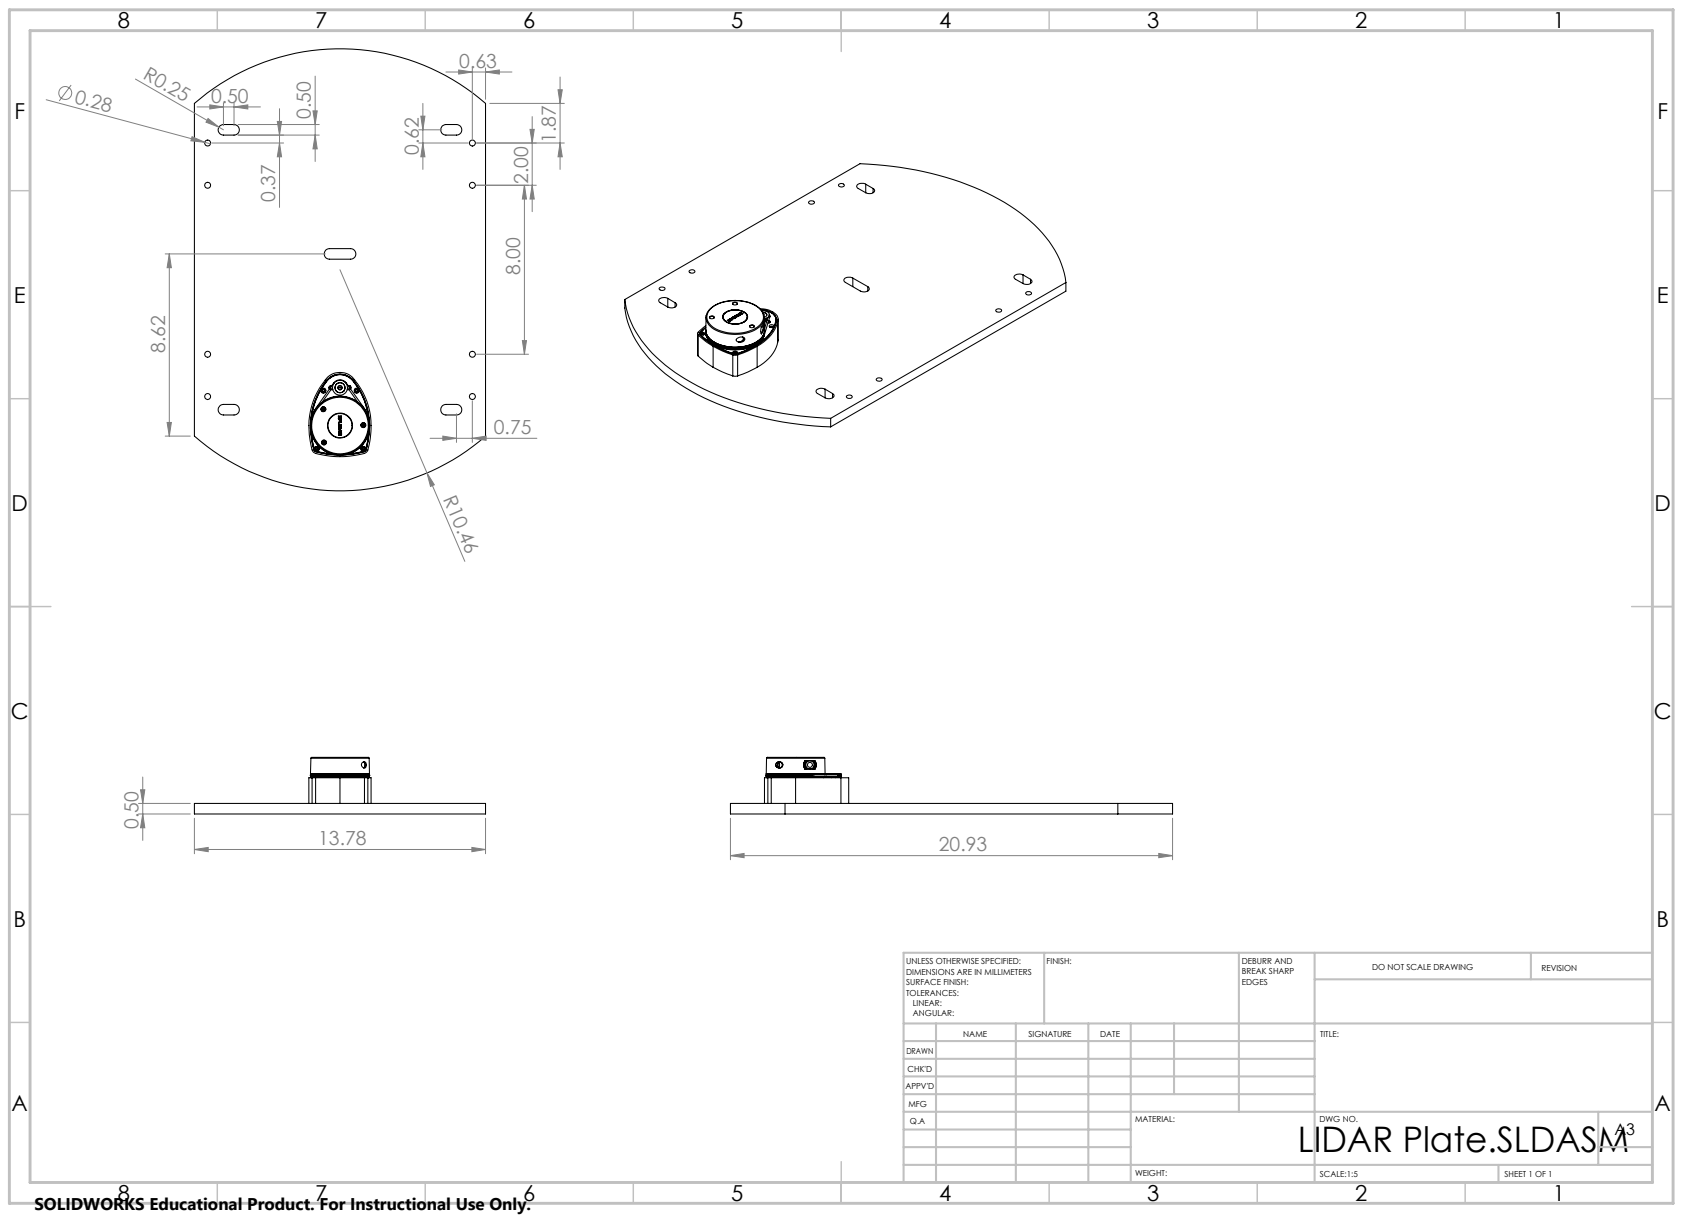
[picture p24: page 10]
FINISH:; DEBURR AND; BREAK SHARP; DO NOT SCALE DRAWING; REVISION

UNLESS OTHERWISE SPECIFIED:
DIMENSIONS ARE IN MILLIMETERS
SURFACE FINISH:
TOLERANCES:
LINEAR:
ANGULAR:

NAME | SIGNATURE | DATE | | TITLE:

DRAWN
CHK'D
APPV'D
MFG

LIDAR Plate.SLDASM

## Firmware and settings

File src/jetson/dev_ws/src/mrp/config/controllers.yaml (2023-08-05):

controller_manager:
  ros__parameters:
    update_rate: 30
    
    diff_cont:
      type: diff_drive_controller/DiffDriveController

    joint_broad:
      type: joint_state_broadcaster/JointStateBroadcaster

diff_cont:
  ros__parameters:
    publish_rate: 30.0
    base_frame_id: base_link
    
    left_wheel_names: ["rear_left_wheel_joint", "front_left_wheel_joint"]
    right_wheel_names: ["rear_right_wheel_joint", "front_right_wheel_joint"]
    # TODO: MUST BE UPDATED MANUALLY
    wheel_separation: 0.4135
    wheel_radius: 0.0762

    use_stamped_vel: false

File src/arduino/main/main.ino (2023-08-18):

#include <SharpIR.h>
#include <util/atomic.h>

/* ----------------------------- Program config ----------------------------- */

#define BAUD_RATE 57600

// Distance in cm at which an IR sensor is considered blocked when moving
// forward or backwards
int LINEAR_CLEAR_THRESHOLD = 20;
// Distance in cm at which an IR sensor is considered blocked when turning
int TURN_CLEAR_THRESHOLD = 15;

// Time in milliseconds to continue the last command before stopping, in absence
// of a new command.
unsigned COMMAND_TIMEOUT = 1000;
// Should always be greater than 30 ms to prevent an internal delay in SharpIR.
const unsigned IR_POLL = 200;

// ACS712 ammeter constants
const float AMMETER_VOLTAGE = 5.0;
const float AMMETER_SENSITIVITY = 0.066;
const int AMMETER_MAX = 1024;   // Ammeter raw value is in range [0, 1024]
const float MIN_CURRENT = 0.25; // Values below this are treated as 0 amps

// Lookup tables for motor response; represents small decimals as shorts, i.e. 12.47 -> 1247
const short FL_LOOKUP_F[256] = {0, 0, 0, 0, 0, 0, 0, 0, 0, 0, 0, 0, 0, 0, 42, 61, 79, 103, 121, 145, 176, 203, 227, 252, 270, 308, 329, 363, 394, 422, 451, 478, 506, 534, 565, 595, 624, 651, 682, 710, 740, 766, 794, 823, 856, 879, 908, 932, 955, 984, 1012, 1037, 1063, 1090, 1113, 1141, 1166, 1192, 1213, 1237, 1260, 1285, 1310, 1334, 1355, 1373, 1400, 1417, 1440, 1458, 1479, 1502, 1522, 1543, 1557, 1580, 1597, 1615, 1636, 1654, 1669, 1690, 1710, 1710, 1745, 1767, 1779, 1799, 1812, 1825, 1836, 1859, 1866, 1885, 1893, 1914, 1918, 1938, 1952, 1967, 1975, 1992, 2004, 2014, 2023, 2039, 2044, 2061, 2072, 2072, 2089, 2098, 2111, 2113, 2128, 2135, 2147, 2160, 2169, 2172, 2184, 2193, 2195, 2206, 2221, 2221, 2228, 2243, 2253, 2260, 2268, 2275, 2279, 2281, 2300, 2303, 2314, 2320, 2327, 2329, 2338, 2345, 2355, 2361, 2359, 2373, 2381, 2386, 2387, 2398, 2402, 2404, 2415, 2416, 2424, 2426, 2436, 2444, 2445, 2453, 2453, 2450, 2464, 2472, 2470, 2477, 2482, 2484, 2485, 2493, 2495, 2490, 2504, 2510, 2506, 2515, 2522, 2523, 2529, 2531, 2534, 2532, 2542, 2536, 2546, 2546, 2551, 2553, 2558, 2562, 2561, 2569, 2574, 2577, 2580, 2580, 2578, 2586, 2592, 2595, 2588, 2602, 2604, 2599, 2609, 2611, 2610, 2616, 2617, 2618, 2621, 2626, 2627, 2628, 2633, 2635, 2638, 2642, 2643, 2641, 2650, 2653, 2652, 2653, 2657, 2652, 2656, 2664, 2662, 2664, 2666, 2673, 2672, 2678, 2678, 2681, 2679, 2685, 2685, 2687, 2693, 2697, 2697, 2699, 2702, 2699, 2707, 2708, 2708, 2714, 2721, 2722, 2728, 2741, 2755, 2784};
const short FR_LOOKUP_F[256] = {0, 0, 0, 0, 0, 0, 0, 0, 0, 0, 0, 0, 0, 0, 49, 93, 121, 147, 170, 197, 224, 257, 283, 308, 347, 376, 405, 432, 466, 493, 524, 553, 583, 614, 645, 670, 704, 730, 762, 792, 819, 856, 880, 896, 924, 959, 988, 1021, 1045, 1061, 1100, 1124, 1140, 1173, 1179, 1218, 1247, 1270, 1295, 1322, 1306, 1340, 1384, 1400, 1428, 1443, 1476, 1495, 1493, 1533, 1554, 1573, 1595, 1616, 1624, 1649, 1670, 1677, 1684, 1711, 1725, 1718, 1768, 1761, 1745, 1809, 1829, 1842, 1857, 1823, 1882, 1901, 1899, 1930, 1921, 1947, 1955, 1955, 1963, 2000, 1995, 2020, 2035, 2007, 2059, 2053, 2079, 2067, 2088, 2104, 2116, 2132, 2135, 2133, 2152, 2158, 2165, 2172, 2182, 2176, 2203, 2215, 2200, 2211, 2235, 2236, 2239, 2258, 2255, 2262, 2283, 2286, 2285, 2299, 2304, 2283, 2294, 2322, 2326, 2336, 2331, 2338, 2352, 2361, 2366, 2362, 2370, 2376, 2376, 2372, 2395, 2399, 2396, 2393, 2409, 2409, 2415, 2423, 2425, 2426, 2442, 2439, 2450, 2447, 2458, 2463, 2468, 2442, 2470, 2479, 2473, 2477, 2486, 2491, 2489, 2501, 2503, 2495, 2508, 2497, 2515, 2514, 2526, 2525, 2516, 2534, 2526, 2535, 2543, 2543, 2534, 2551, 2546, 2554, 2554, 2562, 2555, 2565, 2567, 2568, 2557, 2578, 2565, 2580, 2574, 2587, 2573, 2584, 2594, 2593, 2595, 2594, 2599, 2600, 2599, 2599, 2608, 2615, 2616, 2605, 2620, 2622, 2616, 2615, 2628, 2627, 2628, 2635, 2635, 2634, 2637, 2642, 2633, 2641, 2647, 2647, 2649, 2655, 2654, 2657, 2660, 2664, 2661, 2658, 2669, 2668, 2673, 2678, 2675, 2682, 2686, 2687, 2691, 2710, 2722, 2739};
const short RL_LOOKUP_F[256] = {0, 0, 0, 0, 0, 0, 0, 0, 0, 0, 0, 0, 18, 38, 56, 74, 89, 111, 126, 147, 167, 187, 205, 226, 248, 266, 284, 310, 325, 350, 371, 391, 411, 432, 457, 474, 497, 520, 537, 560, 589, 613, 631, 661, 687, 713, 757, 775, 794, 806, 826, 844, 859, 889, 906, 928, 944, 968, 983, 1009, 1023, 1039, 1063, 1074, 1101, 1121, 1183, 1179, 1201, 1223, 1238, 1260, 1283, 1302, 1302, 1321, 1344, 1359, 1383, 1397, 1425, 1440, 1455, 1476, 1484, 1508, 1521, 1532, 1558, 1573, 1583, 1602, 1614, 1623, 1648, 1640, 1673, 1680, 1710, 1711, 1709, 1739, 1743, 1771, 1789, 1784, 1811, 1825, 1838, 1848, 1846, 1873, 1888, 1890, 1908, 1912, 1929, 1937, 1953, 1954, 1969, 1988, 1989, 1987, 2015, 2023, 2011, 2027, 2039, 2053, 2068, 2063, 2086, 2085, 2105, 2104, 2105, 2120, 2125, 2128, 2134, 2144, 2145, 2170, 2172, 2173, 2177, 2189, 2197, 2200, 2202, 2207, 2217, 2213, 2219, 2235, 2251, 2241, 2249, 2255, 2276, 2270, 2286, 2290, 2299, 2304, 2308, 2306, 2311, 2314, 2329, 2324, 2332, 2338, 2331, 2340, 2353, 2344, 2342, 2361, 2370, 2376, 2373, 2387, 2388, 2393, 2398, 2396, 2409, 2411, 2406, 2422, 2417, 2416, 2429, 2420, 2436, 2440, 2438, 2449, 2443, 2454, 2454, 2457, 2469, 2469, 2459, 2471, 2476, 2475, 2485, 2493, 2494, 2492, 2498, 2500, 2494, 2511, 2508, 2510, 2519, 2515, 2523, 2527, 2525, 2530, 2530, 2537, 2528, 2547, 2550, 2548, 2549, 2550, 2554, 2566, 2561, 2569, 2572, 2575, 2573, 2583, 2588, 2587, 2581, 2586, 2603, 2610, 2606, 2616, 2622, 2632, 2640, 2659, 2673, 2698};
const short RR_LOOKUP_F[256] = {0, 0, 0, 0, 0, 0, 0, 0, 0, 0, 0, 0, 0, 38, 59, 86, 110, 130, 152, 182, 208, 237, 256, 291, 317, 348, 373, 402, 428, 462, 493, 522, 552, 582, 613, 640, 672, 703, 726, 758, 789, 818, 830, 872, 898, 934, 959, 989, 1016, 1040, 1065, 1070, 1104, 1137, 1163, 1190, 1214, 1229, 1270, 1286, 1325, 1307, 1332, 1357, 1400, 1434, 1458, 1460, 1501, 1507, 1536, 1569, 1587, 1601, 1629, 1641, 1654, 1683, 1702, 1699, 1709, 1756, 1769, 1784, 1805, 1793, 1779, 1838, 1867, 1860, 1837, 1912, 1864, 1929, 1887, 1959, 1948, 1945, 1952, 1961, 1977, 2014, 2032, 2045, 2071, 2068, 2081, 2066, 2117, 2101, 2136, 2145, 2145, 2154, 2158, 2181, 2186, 2148, 2205, 2186, 2219, 2211, 2222, 2229, 2253, 2241, 2246, 2279, 2277, 2291, 2295, 2262, 2308, 2310, 2326, 2309, 2338, 2323, 2327, 2354, 2365, 2360, 2373, 2380, 2378, 2388, 2392, 2392, 2389, 2394, 2414, 2424, 2402, 2435, 2429, 2419, 2432, 2443, 2433, 2461, 2445, 2457, 2467, 2466, 2478, 2483, 2486, 2480, 2468, 2495, 2486, 2498, 2502, 2445, 2471, 2515, 2527, 2504, 2526, 2519, 2541, 2541, 2546, 2542, 2547, 2554, 2561, 2554, 2549, 2552, 2562, 2571, 2556, 2568, 2579, 2580, 2581, 2589, 2597, 2596, 2595, 2605, 2608, 2593, 2609, 2613, 2600, 2591, 2618, 2622, 2617, 2627, 2621, 2618, 2639, 2627, 2639, 2646, 2647, 2639, 2655, 2648, 2647, 2646, 2654, 2649, 2638, 2667, 2668, 2668, 2677, 2677, 2676, 2667, 2683, 2681, 2684, 2692, 2691, 2693, 2697, 2703, 2700, 2702, 2706, 2706, 2714, 2717, 2713, 2717, 2725, 2732, 2732, 2753, 2769, 2787};

const short FL_LOOKUP_R[256] = {0, 0, 0, 0, 0, 0, 0, 0, 0, 0, 0, 0, 0, 0, 31, 59, 84, 111, 136, 157, 185, 213, 241, 280, 307, 341, 370, 401, 434, 464, 504, 533, 570, 600, 629, 662, 696, 724, 757, 787, 814, 851, 875, 906, 936, 971, 996, 1027, 1050, 1087, 1107, 1132, 1164, 1191, 1221, 1246, 1270, 1290, 1319, 1340, 1369, 1396, 1422, 1439, 1468, 1495, 1511, 1529, 1549, 1571, 1593, 1613, 1632, 1640, 1668, 1687, 1709, 1710, 1728, 1752, 1768, 1791, 1797, 1811, 1834, 1858, 1857, 1877, 1888, 1900, 1921, 1931, 1946, 1955, 1959, 1983, 1993, 2019, 2032, 2029, 2041, 2067, 2079, 2087, 2091, 2098, 2117, 2123, 2132, 2143, 2144, 2158, 2167, 2183, 2196, 2193, 2207, 2223, 2233, 2238, 2246, 2249, 2266, 2267, 2282, 2283, 2291, 2298, 2309, 2318, 2323, 2317, 2329, 2335, 2347, 2350, 2361, 2365, 2370, 2377, 2378, 2384, 2400, 2401, 2401, 2411, 2409, 2417, 2425, 2428, 2429, 2436, 2447, 2451, 2447, 2455, 2464, 2464, 2471, 2478, 2481, 2484, 2488, 2488, 2495, 2500, 2504, 2503, 2504, 2509, 2513, 2524, 2524, 2523, 2531, 2534, 2533, 2541, 2547, 2545, 2547, 2549, 2554, 2558, 2560, 2569, 2566, 2575, 2578, 2575, 2584, 2588, 2582, 2588, 2593, 2595, 2595, 2600, 2608, 2605, 2614, 2615, 2617, 2617, 2620, 2620, 2624, 2627, 2631, 2632, 2632, 2638, 2631, 2643, 2645, 2644, 2648, 2656, 2652, 2655, 2655, 2654, 2660, 2664, 2665, 2661, 2666, 2666, 2667, 2675, 2679, 2675, 2681, 2680, 2686, 2687, 2685, 2687, 2688, 2689, 2691, 2689, 2699, 2700, 2702, 2707, 2709, 2707, 2711, 2714, 2717, 2719, 2728, 2734, 2749, 2783};
const short FR_LOOKUP_R[256] = {0, 0, 0, 0, 0, 0, 0, 0, 0, 0, 0, 0, 0, 45, 69, 97, 115, 146, 175, 206, 230, 257, 291, 328, 355, 377, 420, 447, 481, 514, 543, 576, 602, 635, 591, 651, 717, 758, 796, 754, 820, 811, 897, 920, 940, 992, 1017, 1029, 1064, 1087, 1139, 1118, 1147, 1189, 1230, 1255, 1240, 1253, 1290, 1340, 1311, 1402, 1398, 1407, 1450, 1472, 1479, 1532, 1552, 1553, 1519, 1587, 1568, 1583, 1644, 1660, 1656, 1711, 1724, 1736, 1766, 1729, 1738, 1791, 1809, 1831, 1805, 1860, 1847, 1895, 1873, 1906, 1922, 1951, 1949, 1900, 1936, 1936, 1963, 2001, 2007, 2007, 2029, 2063, 2045, 2040, 2064, 2100, 2106, 2079, 2108, 2124, 2109, 2125, 2134, 2160, 2158, 2155, 2188, 2158, 2174, 2209, 2216, 2194, 2222, 2199, 2245, 2222, 2245, 2268, 2267, 2275, 2251, 2253, 2282, 2257, 2290, 2279, 2287, 2267, 2315, 2304, 2315, 2317, 2336, 2364, 2339, 2342, 2375, 2355, 2371, 2388, 2386, 2400, 2375, 2384, 2376, 2404, 2416, 2418, 2413, 2420, 2414, 2433, 2441, 2421, 2448, 2443, 2455, 2442, 2449, 2464, 2455, 2461, 2462, 2472, 2461, 2459, 2473, 2481, 2477, 2497, 2502, 2494, 2511, 2494, 2499, 2510, 2504, 2508, 2525, 2532, 2521, 2508, 2520, 2538, 2509, 2539, 2537, 2535, 2519, 2544, 2548, 2549, 2557, 2553, 2559, 2545, 2560, 2571, 2570, 2569, 2554, 2572, 2582, 2572, 2579, 2580, 2590, 2595, 2574, 2591, 2589, 2602, 2592, 2598, 2592, 2599, 2605, 2597, 2611, 2606, 2624, 2606, 2610, 2622, 2631, 2632, 2618, 2632, 2624, 2624, 2634, 2628, 2643, 2653, 2653, 2658, 2644, 2655, 2663, 2658, 2670, 2687, 2705, 2722};
const short RL_LOOKUP_R[256] = {0, 0, 0, 0, 0, 0, 0, 0, 0, 0, 0, 0, 0, 43, 66, 81, 105, 123, 150, 170, 193, 215, 241, 267, 282, 310, 333, 361, 383, 411, 437, 461, 481, 507, 534, 557, 582, 599, 633, 654, 681, 703, 727, 752, 778, 805, 828, 855, 900, 916, 939, 954, 976, 986, 1014, 1039, 1061, 1082, 1103, 1113, 1144, 1164, 1188, 1203, 1221, 1245, 1266, 1274, 1314, 1340, 1356, 1372, 1380, 1383, 1419, 1440, 1445, 1483, 1494, 1506, 1530, 1548, 1545, 1549, 1580, 1608, 1627, 1642, 1654, 1662, 1692, 1705, 1711, 1717, 1737, 1760, 1763, 1785, 1798, 1796, 1827, 1831, 1843, 1849, 1880, 1876, 1899, 1901, 1904, 1927, 1951, 1940, 1957, 1962, 1979, 1979, 1984, 2015, 2021, 2024, 2015, 2051, 2047, 2054, 2068, 2083, 2100, 2110, 2095, 2114, 2120, 2142, 2135, 2145, 2147, 2170, 2180, 2174, 2194, 2212, 2202, 2201, 2229, 2216, 2247, 2224, 2240, 2237, 2259, 2247, 2270, 2268, 2283, 2285, 2264, 2305, 2308, 2317, 2315, 2308, 2334, 2342, 2332, 2344, 2335, 2354, 2357, 2358, 2372, 2370, 2356, 2375, 2383, 2389, 2369, 2402, 2412, 2405, 2411, 2421, 2397, 2420, 2432, 2435, 2419, 2425, 2439, 2450, 2451, 2450, 2503, 2494, 2478, 2476, 2472, 2480, 2466, 2481, 2494, 2501, 2504, 2501, 2505, 2505, 2512, 2512, 2525, 2513, 2521, 2527, 2512, 2532, 2534, 2535, 2537, 2543, 2549, 2543, 2549, 2562, 2557, 2547, 2564, 2567, 2570, 2569, 2574, 2576, 2580, 2584, 2588, 2590, 2587, 2590, 2599, 2602, 2602, 2600, 2608, 2612, 2613, 2616, 2619, 2620, 2626, 2630, 2637, 2625, 2643, 2643, 2654, 2661, 2677, 2688, 2704, 2730};
const short RR_LOOKUP_R[256] = {0, 0, 0, 0, 0, 0, 0, 0, 0, 0, 0, 0, 0, 0, 0, 88, 120, 142, 167, 195, 226, 260, 294, 318, 358, 389, 421, 451, 486, 511, 547, 573, 615, 646, 669, 698, 739, 763, 794, 829, 855, 889, 895, 946, 962, 1003, 1035, 1046, 1094, 1121, 1123, 1142, 1191, 1214, 1211, 1251, 1305, 1310, 1335, 1362, 1394, 1428, 1442, 1443, 1463, 1500, 1471, 1548, 1566, 1551, 1554, 1629, 1598, 1648, 1656, 1705, 1692, 1728, 1726, 1773, 1777, 1758, 1807, 1812, 1826, 1838, 1848, 1841, 1910, 1909, 1903, 1924, 1962, 1844, 1994, 1965, 1885, 1984, 2048, 2038, 2012, 1996, 2071, 2090, 2099, 2113, 2087, 2087, 2143, 2152, 2095, 2151, 2107, 2181, 2165, 2201, 2142, 2199, 2221, 2240, 2224, 2225, 2237, 2249, 2211, 2182, 2211, 2242, 2302, 2272, 2330, 2219, 2295, 2326, 2330, 2290, 2351, 2364, 2355, 2342, 2336, 2233, 2401, 2384, 2372, 2367, 2398, 2390, 2424, 2380, 2403, 2435, 2460, 2450, 2448, 2457, 2447, 2468, 2463, 2473, 2462, 2490, 2477, 2445, 2492, 2485, 2486, 2500, 2508, 2422, 2514, 2499, 2514, 2533, 2539, 2526, 2537, 2536, 2551, 2543, 2559, 2559, 2564, 2570, 2570, 2565, 2564, 2567, 2584, 2566, 2581, 2580, 2572, 2573, 2590, 2596, 2593, 2596, 2597, 2602, 2606, 2611, 2609, 2597, 2597, 2597, 2617, 2623, 2633, 2635, 2624, 2638, 2592, 2638, 2626, 2640, 2648, 2638, 2647, 2643, 2652, 2638, 2653, 2664, 2668, 2654, 2649, 2677, 2671, 2663, 2665, 2666, 2677, 2680, 2683, 2679, 2690, 2680, 2684, 2681, 2697, 2693, 2707, 2703, 2699, 2714, 2721, 2714, 2721, 2724, 2728, 2731, 2744, 2751, 2764, 2790};

/* ---------------------------- Arduino pin setup --------------------------- */

// Pins for connection to the left motor driver
const int L_ENA = 5; // fl
const int L_ENB = 6; // rl
const int L_INT1 = 44;
const int L_INT2 = 46;
const int L_INT3 = 48;
const int L_INT4 = 50;

// Pins for connection to the right motor driver
const int R_ENA = 2; // fr
const int R_ENB = 3; // rr
const int R_INT1 = 45;
const int R_INT2 = 47;
const int R_INT3 = 49;
const int R_INT4 = 51;

// Pins for the encoders
const int FL_ENC = 18;
const int FR_ENC = 20;
const int RL_ENC = 19;
const int RR_ENC = 21;

// Model ID for the IR sensors, used internally in SharpIR
#define model SharpIR::GP2Y0A21YK0F

// Sets up the IR sensors, second argument is the pin they're connected to
SharpIR IR_FL(model, A1);
SharpIR IR_FC(model, A2);
SharpIR IR_FR(model, A3);
SharpIR IR_RL(model, A4);
SharpIR IR_RR(model, A5);

// Pin for the ammeter
#define AMMETER_PIN A0

/* ------------------------------ Program data ------------------------------ */

// Tracks whether the motors have been told to move forward or backwards, which
// is only used for the encoders. Updated when PWM is set, remains unchanged
// when robot is ordered to stop.
bool fl_moving_forward = true;
bool fr_moving_forward = true;
bool rl_moving_forward = true;
bool rr_moving_forward = true;

// Timestamp in milliseconds of the last command
unsigned long lastCmdTime = 0;
// Timestamp in milliseconds of the last IR check
unsigned long lastIRTime = 0;

// IR sensor data
int fl_dist, fc_dist, fr_dist, rl_dist, rr_dist;

// Whether the IR sensors are blocked for the current movement
bool ir_blocked = true;

// Any access to these variables must be wrapped in an ATOMIC_BLOCK to prevent
// interrupts mid-read, since they are larger than 1 byte.
volatile long fl_ticks, fr_ticks, rl_ticks, rr_ticks;

// Whether the robot is trying to executing a movement command
bool moving = false;

// Inelegant solution to make checkClear accessible from loop()
int global_fl_pwm = 0, global_fr_pwm = 0;

/* -------------------------------- Encoders -------------------------------- */

// Since the encoders only register ticks, not direction, these tick functions
// fudge the direction by looking at whether the robot was last told to move
// forward or backwards. This won't catch movement in a different direction than
// expected, but that's rare.

void FL_tick() {
    if (fl_moving_forward) {
        fl_ticks++;
    } else {
        fl_ticks--;
    }
}

void FR_tick() {
    if (fr_moving_forward) {
        fr_ticks++;
    } else {
        fr_ticks--;
    }
}

void RL_tick() {
    if (rl_moving_forward) {
        rl_ticks++;
    } else {
        rl_ticks--;
    }
}

void RR_tick() {
    if (rr_moving_forward) {
        rr_ticks++;
    } else {
        rr_ticks--;
    }
}

/* ------------------------------- IR Sensors ------------------------------- */

void updateIR() {
    fl_dist = IR_FL.getDistance();
    fc_dist = IR_FC.getDistance();
    fr_dist = IR_FR.getDistance();
    rl_dist = IR_RL.getDistance();
    rr_dist = IR_RR.getDistance();
}

bool frontClear() {
    return fl_dist > LINEAR_CLEAR_THRESHOLD &&
           fc_dist > LINEAR_CLEAR_THRESHOLD &&
           fr_dist > LINEAR_CLEAR_THRESHOLD;
}

bool backClear() {
    return rl_dist > LINEAR_CLEAR_THRESHOLD &&
           rr_dist > LINEAR_CLEAR_THRESHOLD;
}

bool areaClear() {
    return fl_dist > TURN_CLEAR_THRESHOLD &&
           fc_dist > TURN_CLEAR_THRESHOLD &&
           fr_dist > TURN_CLEAR_THRESHOLD &&
           rl_dist > TURN_CLEAR_THRESHOLD &&
           rr_dist > TURN_CLEAR_THRESHOLD;
}

void checkClear() {
    // If not turning
    if (global_fl_pwm == global_fr_pwm) {
        if (global_fl_pwm > 0 && !frontClear()) {
            // If moving forward and front is not clear
            ir_blocked = true;
        } else if (global_fl_pwm < 0 && !backClear()) {
            // If moving backwards and rear is not clear
            ir_blocked = true;
        } else {
            ir_blocked = false;
        }
    } else if (!areaClear()) {
        // If turning and area is not clear
        ir_blocked = true;
    } else {
        ir_blocked = false;
    }
}

/* --------------------------------- Motors --------------------------------- */

int lookup_pwm(const short lookup_table[], float velocity) {
    short vel_short = short(velocity * 100);

    // Edge cases
    if (vel_short == 0) {
        return 0;
    } else if (vel_short >= lookup_table[255]) {
        return 255;
    }

    // Modified binary search
    int left = 0;
    int right = 255;

    while (left <= right) {
        int mid = (left + right) / 2;

        if (lookup_table[mid] < vel_short) {
            left = mid + 1;
        } else if (lookup_table[mid] > vel_short) {
            right = mid - 1;
        } else {
            return mid;
        }
    }

    // Exact velocity not found, which is likely, so return nearest
    if (abs(lookup_table[left] - vel_short) < abs(lookup_table[right] - vel_short)) {
        return left;
    } else {
        return right;
    }
}

void set_pwm(int fl_pwm, int fr_pwm, int rl_pwm, int rr_pwm) {
    if (fl_pwm == 0 && fr_pwm == 0 && rl_pwm == 0 && rr_pwm == 0) {
        moving = false;
    } else if (!moving) {
        // Ensures that the IRs are checked when starting to move

        global_fl_pwm = fl_pwm;
        global_fr_pwm = fr_pwm;

        lastIRTime = millis();
        updateIR();
        checkClear();

        moving = true;
    }

    // If the IRs are blocked, cancel the movement command
    if (ir_blocked) {
        fl_pwm = 0;
        fr_pwm = 0;
        rl_pwm = 0;
        rr_pwm = 0;
        moving = false;
    }

    global_fl_pwm = fl_pwm;
    global_fr_pwm = fr_pwm;

    // Front left
    if (fl_pwm > 0) {
        // Forward
        digitalWrite(L_INT1, 1);
        digitalWrite(L_INT2, 0);

        fl_moving_forward = true;
    } else if (fl_pwm < 0) {
        // Backward
        digitalWrite(L_INT1, 0);
        digitalWrite(L_INT2, 1);

        fl_moving_forward = false;
    } else {
        // Stop
        digitalWrite(L_INT1, 0);
        digitalWrite(L_INT2, 0);

        // fl_moving_forward remains at its last value to account for drift
    }

    analogWrite(L_ENA, abs(fl_pwm));

    // Front right
    if (fr_pwm > 0) {
        // Forward
        digitalWrite(R_INT1, 1);
        digitalWrite(R_INT2, 0);

        fr_moving_forward = true;
    } else if (fr_pwm < 0) {
        // Backward
        digitalWrite(R_INT1, 0);
        digitalWrite(R_INT2, 1);

        fr_moving_forward = false;
    } else {
        // Stop
        digitalWrite(R_INT1, 0);
        digitalWrite(R_INT2, 0);
    }

    analogWrite(R_ENA, abs(fr_pwm));

    // Rear left
    if (rl_pwm > 0) {
        // Forward
        digitalWrite(L_INT3, 1);
        digitalWrite(L_INT4, 0);

        rl_moving_forward = true;
    } else if (rl_pwm < 0) {
        // Backward
        digitalWrite(L_INT3, 0);
        digitalWrite(L_INT4, 1);

        rl_moving_forward = false;
    } else {
        // Stop
        digitalWrite(L_INT3, 0);
        digitalWrite(L_INT4, 0);
    }

    analogWrite(L_ENB, abs(rl_pwm));

    // Rear right
    if (rr_pwm > 0) {
        // Forward
        digitalWrite(R_INT3, 0);
        digitalWrite(R_INT4, 1);

        rr_moving_forward = true;
    } else if (rr_pwm < 0) {
        // Backward
        digitalWrite(R_INT3, 1);
        digitalWrite(R_INT4, 0);

        rr_moving_forward = false;
    } else {
        // Stop
        digitalWrite(R_INT3, 0);
        digitalWrite(R_INT4, 0);
    }

    analogWrite(R_ENB, abs(rr_pwm));
}
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
void loop() {
    if (Serial.available() > 0) {
        // Reads the first character of the message
        char cmd_sel = Serial.read();
        float arg[4] = {0, 0, 0, 0};
        short num_args = 0;

        // Determines how many arguments should be parsed based on command
        if (cmd_sel == 'p' || cmd_sel == 'm') {
            num_args = 4;
        } else if (cmd_sel == 'd') {
            num_args = 2;
        } else if (cmd_sel == 't') {
            num_args = 1;
        }

        // Reads num_args many floats from the message
        for (int i = 0; i < num_args; i++) {
            arg[i] = Serial.parseFloat();
        }

        // Consume the remainder of the message
        Serial.readStringUntil('\n');

        run_command(cmd_sel, arg[0], arg[1], arg[2], arg[3]);
    }

    unsigned long current_time = millis();

    if (moving) {
        if (current_time - lastCmdTime > COMMAND_TIMEOUT) {
            // Stops robot if COMMAND_TIMEOUT ms have elapsed since the last command
            set_pwm(0, 0, 0, 0);
        }

        if (current_time - lastIRTime > IR_POLL) {
            // Checks the IR sensors if it has been at least IR_POLL ms since the last check
            lastIRTime = current_time;

            updateIR();
            checkClear();

            if (ir_blocked) {
                set_pwm(0, 0, 0, 0);
            }
        }
    }
}

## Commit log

2023-05-21 initial commit for motors v2
2023-05-21 minor refactor of motor control in separate file
2023-05-27 replaced socket server with Flask
2023-05-28 corrected some formatting of motors v2
2023-05-28 corrected motors v2 format
2023-05-28 partial refactor of Arduino code
2023-05-29 recoded arduino program
2023-05-29 refactored to account for missing arduino
2023-06-01 renamed arduino program
2023-06-04 refactored jetson code
2023-06-04 minor fixes to arduino program
    [main.ino]
2023-06-08 split requirements between jetson and remote
2023-06-08 corrected inputs to be ints instead of floats
    [main.ino]
2023-06-16 small change to checking sensors
2023-06-17 refactored pin naming
2023-06-17 structured arduino program as arduino project
2023-06-17 changed arduino main to work with ROS, w/o IR
2023-06-22 fixed variable naming error
    [main.ino]
2023-06-29 removed baud rate and set PWM min/max/turn
2023-06-30 added encoder tick publishing
2023-07-03 added ROS odometry example
2023-07-03 added missing UInt16 header file
    [main.ino]
2023-07-03 updated left PWM pins
2023-07-03 fixed int pin setting
    [main.ino]
2023-07-06 fixed PWM constraints
2023-07-06 added direction to encoder ticks
2023-07-13 added encoder value wrapping logic
2023-07-13 untested odometer prototype
2023-07-14 removed nonfunctional debug printing
2023-07-14 corrected error never setting lastIRTime
    [main.ino]
2023-07-14 removed ArduinoController
2023-07-29 initial commit for humble code
    [inertial_macros.xacro, lidar.xacro, mrp_core.xacro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]
2023-07-29 updated Arduino code
2023-08-03 removed encoder tick wrapping logic
2023-08-03 arduino_interface initial commit
2023-08-03 added encoder reset command
    [main.ino]
2023-08-03 modified mrp package to use arduino_interface
    [my_controllers.yaml, robot.urdf.xacro, ros2_control.xacro]
2023-08-04 corrected motor command pins
    [main.ino]
2023-08-04 updated robot dimensions
    [robot.urdf.xacro]
2023-08-05 corrected wheel positioning
    [robot.urdf.xacro]
2023-08-05 corrected bug with launch Command substitution
    [lidar.xacro, mrp_core.xacro, robot.urdf.xacro]
2023-08-05 updated wheel separation
    [my_controllers.yaml]
2023-08-05 corrected wheel offsets
    [mrp_core.xacro]
2023-08-05 corrected encoder count value
    [ros2_control.xacro]
2023-08-05 added PID
2023-08-06 corrected lidar position
    [lidar.xacro]
2023-08-06 added Beauregard PID library
2023-08-06 changed velocity to rad/s
2023-08-06 updated hardware interface
    [ros2_control.xacro]
2023-08-06 added comment
    [ros2_control.xacro]
2023-08-06 corrected param naming and state interface order
    [ros2_control.xacro]
2023-08-07 added arduino dependencies
2023-08-07 corrected bounds on PID output, removed PWM_MIN
    [main.ino]
2023-08-07 corrected encoder counts per rev
    [ros2_control.xacro]
2023-08-07 calibrated PID
2023-08-10 added PWM min constraint
2023-08-11 corrected constrain_pwm's parameter type
    [main.ino]
2023-08-14 added program for motor calibration
2023-08-14 added SLAM
    [mrp_core.xacro]
2023-08-15 added motor testing program
2023-08-16 removed PID, added lookup tables
2023-08-17 inverted lidar
2023-08-17 inverted IR sensor
2023-08-18 increased nav2 turning velocity
2023-08-18 fixed IR sensor logic
    [main.ino]
2023-08-18 added motor response data
    [Motor Response Data.xlsx]
2023-08-19 renamed my_controllers.yaml to controllers.yaml
    [controllers.yaml, ros2_control.xacro]
2023-08-19 removed unnecessary todo
    [ros2_control.xacro]
2023-09-05 added hardware design files
    [1.25 2pin-1.SLDPRT, 1.25 2pin-2.SLDPRT, 1.25 3pinÁ¢Ìù.SLDPRT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]
